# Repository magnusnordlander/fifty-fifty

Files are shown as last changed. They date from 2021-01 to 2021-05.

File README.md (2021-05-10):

# fifty-fifty
A grinder controller for my Mazzer Major

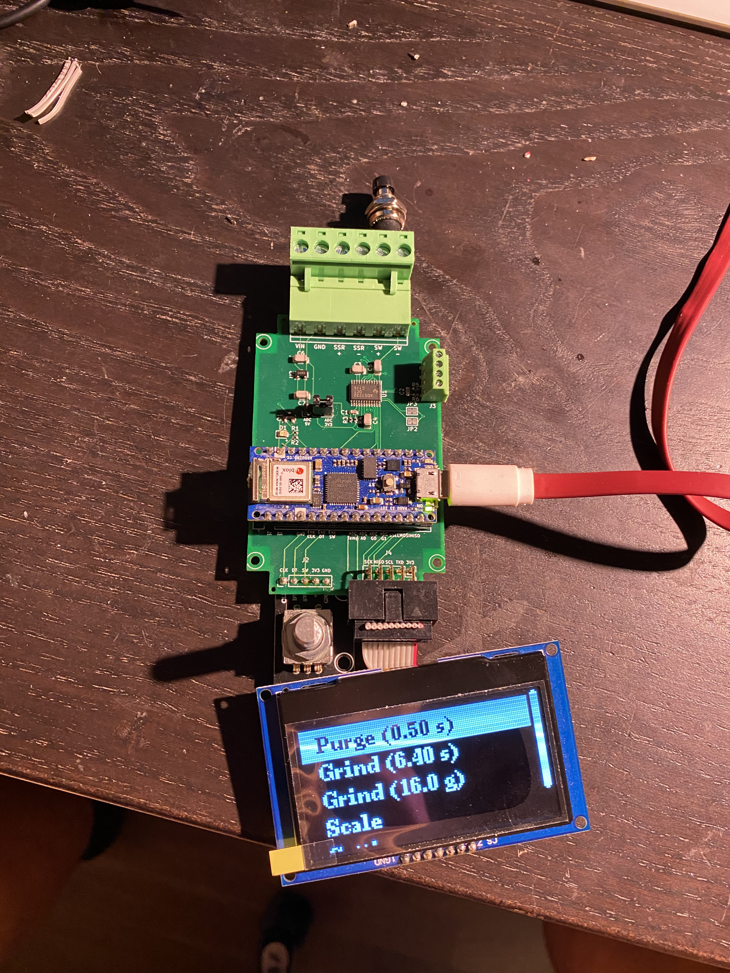
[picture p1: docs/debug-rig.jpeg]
Photo of the debug rig


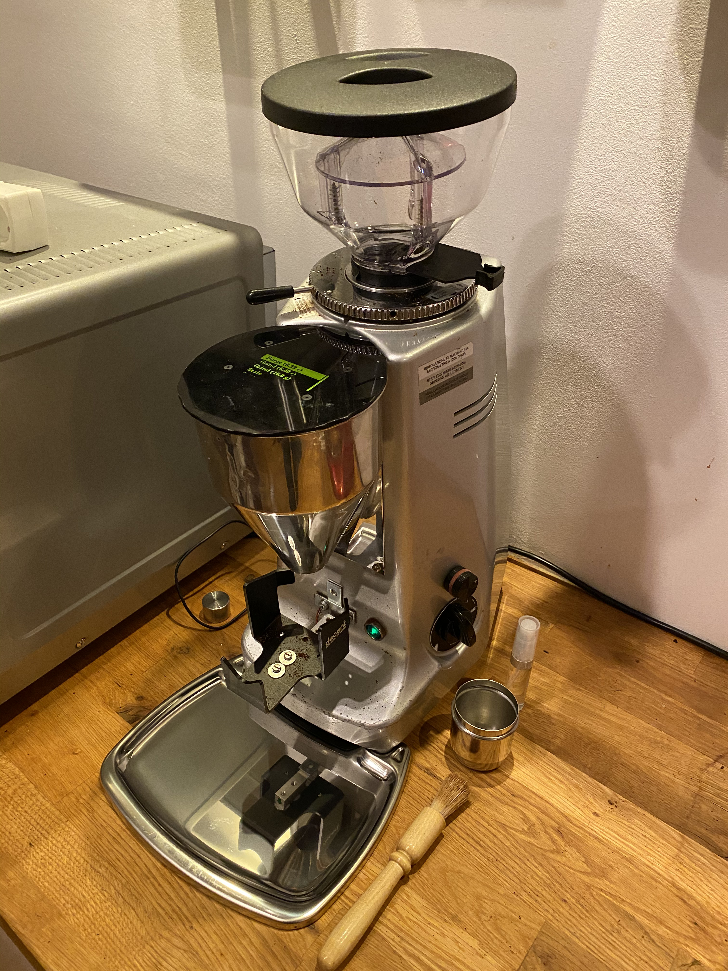
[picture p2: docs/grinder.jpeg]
Photo of the modded grinder


## Status
This project is in use and development. Current PCB Revision is Rev C.

*There will be a Rev D PCB*. The Rev D PCB will adjust the fit for a Futurekit FB20 box (it's currently slightly too large, and the mounting holes are misaligned). 

### Changelog

* Rev A: First revision board
* Rev B: Substantial changes. ADS1232 load cell interface, SMT components, fully populated UEXT connector (was printed).
  * Errata: Resistor R2 never should have existed. Remove R2 or cut trace from R2 to GND.
  * Errata: R3 and R4 silk screens are flipped around. They're the same value though, so it doesn't make any material difference.
* Rev C: Removed the resistor that was R2 in Rev B (hasn't been printed), fixed silk screen, added dots for SMT ICs.
  * Errata: Doesn't quite fit in the intended Futurekit FB20 box.

## Overview

This is an Arduino based grinder controller for my Mazzer Major. It has a display and is controlled by a rotary encoder. It also contains a PCB schematic.

## Features

* Grinder control via a simple to use interface, controlled by a rotary encoder
* Timed grinding
* Grind by weight
  * An ADS1232 load cell interface, sampling a load cell at 80 SPS.
  * High accuracy
  * Fast taring

## Parts

* [Arduino Nano 33 IoT](https://www.electrokit.com/en/product/arduino-nano-33-iot-with-headers/)
* A Solid-state relay
  * I'm using a [Fotek SSR-40 DA clone](https://www.electrokit.com/en/product/solid-state-relay-3-32v-40a/), because that's what came with my used grinder when I bought it
  * If you want a more high-quality component, a [Crydom-Sensata 84137000](http://www.crydom.com/en/products/catalog/gnssr.pdf) would be a good choice
* A high quality 5.3-6.0V power supply. I'm using a [Mean Well RS-15-5](https://www.amazon.se/gp/product/B00MWQD43U/ref=ppx_yo_dt_b_asin_title_o01_s01?ie=UTF8&psc=1). Quality matters for minimizing ADC interference. A 5V power supply with an adjustment potentiometer should do fine, the LDO will regulate anything between 5.3 and 6.0 V to 5V for the ADC. Set your PSU to 5.5V and all will be good.
* A [KY-040 style rotary encoder](https://www.electrokit.com/en/product/rotary-encoder-module/)
* An [SSD1309, SPI connected, 3.3V, 128x64 px OLED](https://www.electrokit.com/produkt/lcd-oled-2-42-12x64px-spi-i2c/)
* A [1000 g whetstone bridge load cell](https://www.electrokit.com/produkt/lastcell-1kg/)

## THT BOM

* 1 x [DIL socket 32 pin (remove 2 pins, optional but recommended)](https://www.electrokit.com/en/product/dil-socket-32-pin/) (For the Arduino)
* 1 x [PCB pin header 5.08mm 6-pole right-angle](https://www.electrokit.com/en/product/pcb-hane-5-08mm-6-pol-vinklad/) (For power, SSR and manual grind knob connection)
* 1 x [IDC box header PCB 10-p 2.54mm](https://www.electrokit.com/en/product/idc-box-header-pcb-10-p-2-54mm/) (For display connection)
* 1 x [Screw terminal 2.54mm 4-pole](https://www.electrokit.com/produkt/skruvplint-2-54mm-4-pol/) (For load cell connection)
* 1 x [5 pin 2.54mm pin header](https://www.electrokit.com/en/product/pin-header-2-54mm-1x40p-red/) (For rotary encoder connection)
* 1 x 3 pin 2.54mm pin header (For ADC debug voltage jumper)
* 1 x [2.54mm jumper](https://www.electrokit.com/produkt/bygel-2-54mm-2p-svart/)

## Anything else?

While not technically part of the board, you'll probably want some other things to make it all work:

* 1 x [Screw terminal pluggable 5.08mm 6-pole](https://www.electrokit.com/en/product/skruvplint-pluggbar-5-08mm-6-pol/)
* 1 x 10 pin IDC flat cable
* 1 x 5 pin jumper wires
* Wiring
  * 0.75 mm² (or higher) copper wiring for the high voltage side
    * Preferably in standard colors, which would be blue/brown in Europe for neutral/load. Signal wire from SSR to the motor can be any other color except green/yellow. Orange is a good choice.
  * Wiring cable, I'd go for 0.20 mm² copper. Preferably in red and black.
* WAGO 221 splicing connectors
* A 100.0 g reference weight for scale calibration

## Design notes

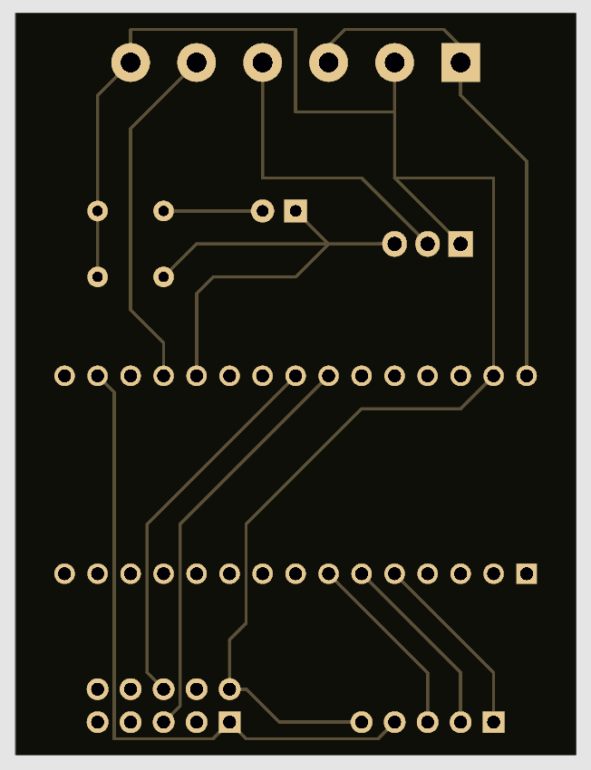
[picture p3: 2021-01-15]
pcb/Back.png

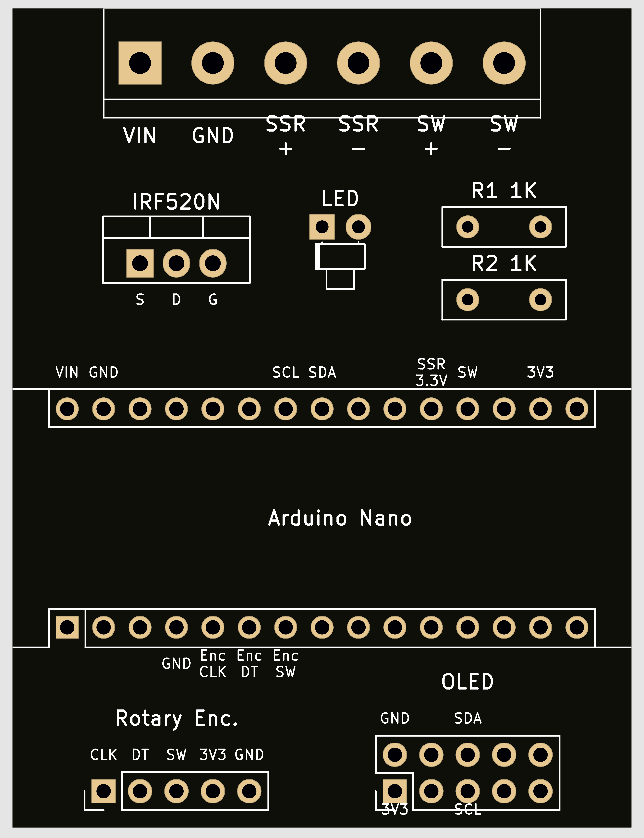
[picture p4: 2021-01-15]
pcb/Front.png

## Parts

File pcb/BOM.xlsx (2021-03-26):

Chip | Name | Package | Purpose | LCSC | Misc
U1 | ADS1232IPWR | TSSOP-24_4.4x7.8x0.65P | ADC | C27919
U2 | XC6206P502MR | SOT-23-3 | LDO | C16767
Q1 | 2N7002 | SOT-23-3 | Mosfet | C8545
D1 | FC-2012HRK-620D | LED_0805 | LED | C84256 | 2V 25 mA
R1 | 0402WGF510JTCE | 0402 | LED limiter | C25125 | 51R
R2 | 0402WGF1000TCE | 0402 | REFP filter | C25076 | 100R
R3 | 0402WGF1000TCE | 0402 | REFN filter | C25076 | 100R
R4 | 0402WGF1000TCE | 0402 | AINP1 filter | C25076 | 100R
R5 | 0402WGF1000TCE | 0402 | AINN1 filter | C25076 | 100R
C1 | CGA3E2C0G1H103JT0Y0N | 0603 | REF filter | C76710 | 10 nF, C0G
C2 | CGA3E2C0G1H103JT0Y0N | 0603 | AIN filter | C76710 | 10 nF, C0G
C3 | GRM31C5C1H104JA01L | 1206 | ADC cap | C97946 | 100 nF, C0G
C4 | GRM31C5C1H104JA01L | 1206 | AVDD filter | C97946 | 100 nF
C5 | GRM31C5C1H104JA01L | 1206 | DVDD filter | C97946 | 100 nF
C6 | GRM31C5C1H104JA01L | 1206 | LDO VI | C97946 | 100 nF
C7 | GRM31C5C1H104JA01L | 1206 | LDO VO | C97946 | 100 nF

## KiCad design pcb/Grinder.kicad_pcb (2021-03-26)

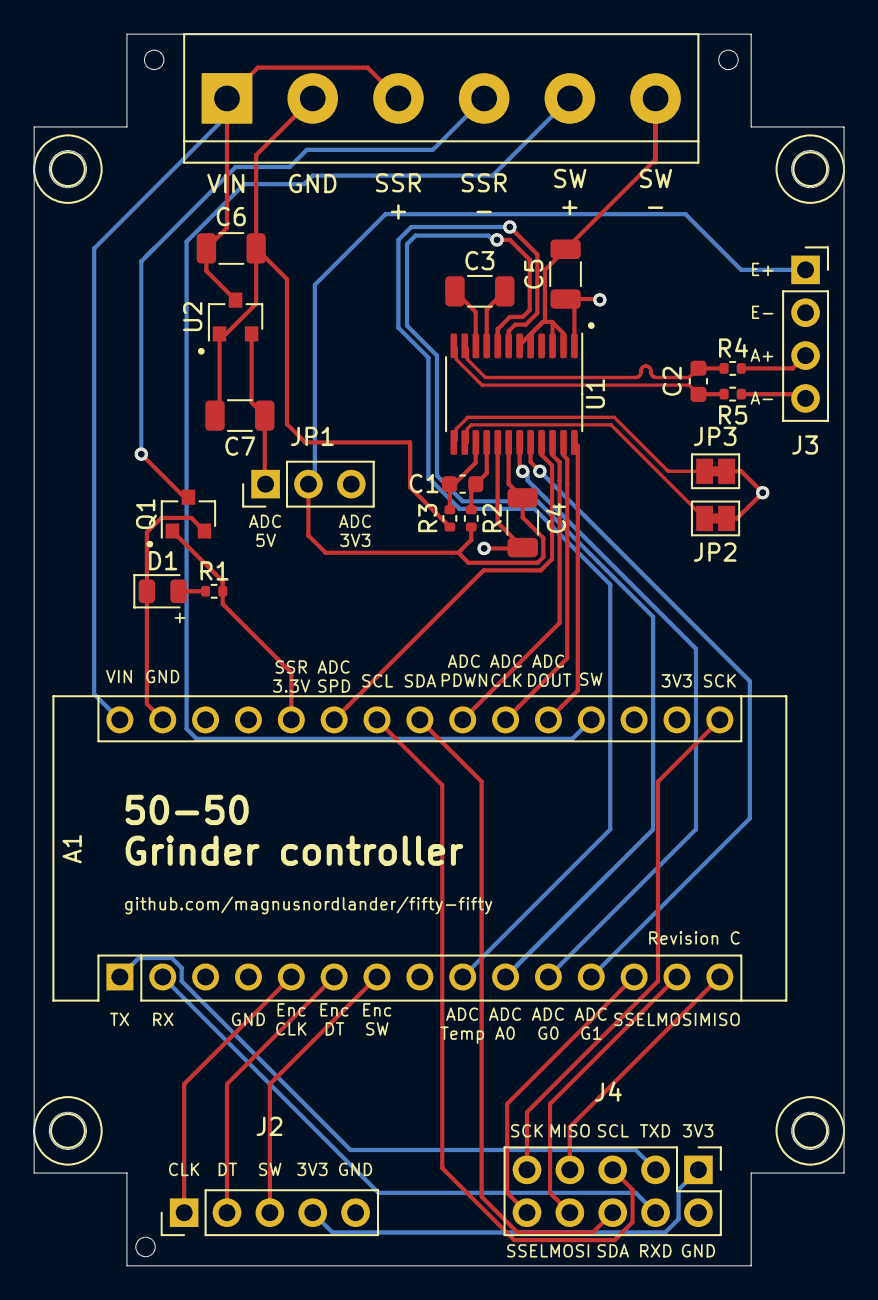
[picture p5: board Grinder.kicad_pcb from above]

Board: 4 copper layers, 48.0 x 73.0 mm, 24 parts (0 on the bottom side), 38 nets.

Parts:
A1: Arduino Nano 33 IoT; Arduino_Nano
C1, C2: 10 nF; C_0603_1608Metric
C3, C5, C6, C7: 100 nF; C_1206_3216Metric
C4: 100nF; C_1206_3216Metric
D1: LED; LED_0805_2012Metric
J1: Conn_01x06; TerminalBlock_bornier-6_P5.08mm
J2: Conn_01x05; PinHeader_1x05_P2.54mm_Vertical
J3: Conn_01x04; PinSocket_1x04_P2.54mm_Vertical
J4: Conn_02x05_Odd_Even; PinHeader_2x05_P2.54mm_Vertical
JP1: Debug voltage; PinHeader_1x03_P2.54mm_Vertical
JP2: AINP2; SolderJumper-2_P1.3mm_Bridged_Pad1.0x1.5mm
JP3: AINN2; SolderJumper-2_P1.3mm_Bridged_Pad1.0x1.5mm
Q1: 2N7002; SOT-23
R1: R; R_0402_1005Metric
R2, R3, R4, R5: 100R; R_0402_1005Metric
U1: ADS1232IPW; TSSOP-24_4.4x7.8mm_P0.65mm
U2: XC6206P502MR; SOT-23

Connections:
3V3: A1.17, C5.1, J2.4, J4.1, JP1.3, U1.1
ADC_A0: A1.10, U1.8
ADC_CLK: A1.21, U1.23
ADC_DOUT: A1.20, U1.24
ADC_GAIN0: A1.11, U1.19
ADC_GAIN1: A1.12, U1.20
ADC_PDWN: A1.22, U1.22
ADC_SPEED: A1.25, U1.21
ADC_TEMP: A1.9, U1.7
AIN1_N: C2.2, R5.1, U1.12
AIN1_P: C2.1, R4.1, U1.11
AIN2_N: JP3.2, U1.13
AIN2_P: JP2.2, U1.14
AVDD: C4.2, J3.1, JP1.2, R2.2, U1.18
ENC_CLK: A1.5, J2.1
ENC_DT: A1.6, J2.2
ENC_SW: A1.7, J2.3
GND: A1.4, A1.29, C4.1, C5.2, C6.2, C7.2, D1.1, J1.2, J1.6, J2.5, J3.2, J4.2, JP2.1, JP3.1, Q1.2, R3.2, U1.2, U1.3, U1.5, U1.6, U1.17, U2.1
MANUAL_SW: A1.19, J1.5
unnamed: C3.1, U1.9
unnamed: C3.2, U1.10
unnamed: C7.1, JP1.1, U2.2
unnamed: D1.2, R1.1
unnamed: J3.3, R4.2
unnamed: J3.4, R5.2
REFN: C1.2, R3.1, U1.15
REFP: C1.1, R2.1, U1.16
SSR_DRAIN: J1.4, Q1.3
SSR_GATE: A1.26, Q1.1, R1.2
UEXT_MISO: A1.15, J4.7
UEXT_MOSI: A1.14, J4.8
UEXT_RX: A1.2, J4.4
UEXT_SCK: A1.16, J4.9
UEXT_SCL: A1.24, J4.5
UEXT_SDA: A1.23, J4.6
UEXT_SSEL: A1.13, J4.10
UEXT_TX: A1.1, J4.3
VIN: A1.30, C6.1, J1.1, J1.3, U2.3

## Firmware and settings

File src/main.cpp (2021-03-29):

#include <Arduino.h>
#include <U8g2lib.h>
#include <Wire.h>
#include <Encoder.h>
#include "NavigationController.h"
#include "ViewControllers/Menus/MenuViewController.h"
#include "ViewControllers/Grinding/ManualGrindViewController.h"
#include "ViewControllers/Settings/PurgeTimeSettingViewController.h"
#include "ViewControllers/Settings/GrindTimeSettingViewController.h"
#include "ViewControllers/Settings/GrindTargetWeightSettingViewController.h"
#include "ViewControllers/Settings/ReactionTimeSettingViewController.h"
#include "ViewControllers/Settings/ScaleDebugViewController.h"
#include "ViewControllers/Grinding/GravimetricGrindViewController.h"
#include "ViewControllers/Settings/ProductivitySettingViewController.h"
#include "ViewControllers/Settings/CalibrationViewController.h"
#include "ViewControllers/Settings/PerformanceDebugViewController.h"
#include "ViewControllers/Grinding/PurgeViewController.h"
#include "ViewControllers/Grinding/TimedGrindViewController.h"
#include "ViewControllers/ScaleViewController.h"
#include "ViewControllers/Menus/MenuItem/ViewControllerMenuItem.h"
#include "ViewControllers/Menus/MenuItem/PopNavigationAndCommitEEPROMMenuItem.h"
#include "ViewControllers/Menus/MenuItem/PurgeMenuItem.h"
#include "ViewControllers/Menus/MenuItem/GrindMenuItem.h"
#include "ViewControllers/Menus/MenuItem/GrindByWeightMenuItem.h"
#include "Settings.h"
#include "ScaleWrapper.h"
#include "ViewControllers/ButtonEvent.h"
#include <types.h>

// DT and CLK must be interrupt pins
#define ENCODER_SW_PIN 4
#define ENCODER_DT_PIN 3
#define ENCODER_CLK_PIN 2

#define MANUAL_GRIND_PIN 14

#define SSR_PIN 21

// DOUT must be interrupt pin
#define ADS1232_PWDN_PIN 17
#define ADS1232_DOUT_PIN 15
#define ADS1232_SCLK_PIN 16
#define ADS1232_TEMP_PIN 6
#define ADS1232_A0_PIN 7
#define ADS1232_GAIN0_PIN 8
#define ADS1232_GAIN1_PIN 9
#define ADS1232_SPEED_PIN 20

// With the exception of CS, these pins are hardware supported
#define UEXT_SPI_CS_PIN 10
#define UEXT_SPI_SCK_PIN 13
#define UEXT_SPI_MISO_PIN 12
#define UEXT_SPI_MOSI_PIN 11
#define UEXT_I2C_SCL_PIN 19
#define UEXT_I2C_SDA_PIN 18

#define SCROLL_DIRECTION 1
// Use I2C SCL as SSD1309 DC and I2C SDA as SSD1309 RES
U8G2_SSD1309_128X64_NONAME0_F_4W_HW_SPI u8g2(U8G2_R2, UEXT_SPI_CS_PIN, UEXT_I2C_SCL_PIN, UEXT_I2C_SDA_PIN);

int Encoder_SW_State = 0;
long Encoder_Diff = 0;
int Manual_Grind_State = HIGH;

long Old_Encoder_Position  = 0;

microtime_t Button_Press_Started_At = 0;

ButtonEvent currentButtonEvent = BUTTON_INACTIVE;

Encoder myEnc(ENCODER_DT_PIN, ENCODER_CLK_PIN);

ScaleWrapper* scale;
SsrState* ssr = nullptr;
ManualGrindViewController* manualGrindView = nullptr;
NavigationController* nav = nullptr;

TimingStruct timings;

void setup(void) {
    pinMode(MANUAL_GRIND_PIN, INPUT_PULLUP);
    pinMode(ENCODER_SW_PIN, INPUT_PULLUP);

    u8g2.begin();

/*
    delay(5000);
    Serial.begin(9600);
    Serial.println("Starting");
    */

    ssr = new SsrState(SSR_PIN);
    auto settings = new Settings();

    pinMode(ADS1232_TEMP_PIN, OUTPUT);
    pinMode(ADS1232_A0_PIN, OUTPUT);
    pinMode(ADS1232_GAIN0_PIN, OUTPUT);
    pinMode(ADS1232_GAIN1_PIN, OUTPUT);
    pinMode(ADS1232_SPEED_PIN, OUTPUT);

    digitalWrite(ADS1232_TEMP_PIN, LOW);
    digitalWrite(ADS1232_A0_PIN, LOW);
    digitalWrite(ADS1232_GAIN0_PIN, HIGH);
    digitalWrite(ADS1232_GAIN1_PIN, HIGH);
    digitalWrite(ADS1232_SPEED_PIN, HIGH);

    scale = ScaleWrapper::GetInstance(ADS1232_DOUT_PIN, ADS1232_SCLK_PIN, ADS1232_PWDN_PIN, settings);

    manualGrindView = new ManualGrindViewController(ssr);

    auto settingsMenu = new MenuViewController(std::vector<MenuItem*> {{
            new ViewControllerMenuItem("Purge time", new PurgeTimeSettingViewController(settings)),
            new ViewControllerMenuItem("Grind time", new GrindTimeSettingViewController(settings)),
            new ViewControllerMenuItem("Target weight", new GrindTargetWeightSettingViewController(settings)),
            new ViewControllerMenuItem("Reaction time", new ReactionTimeSettingViewController(settings)),
            new ViewControllerMenuItem("Productivity", new ProductivitySettingViewController(settings)),
            new ViewControllerMenuItem("Calibrate (100 g)", new CalibrationViewController(settings, scale)),
            new ViewControllerMenuItem("Scale debug", new ScaleDebugViewController(scale)),
            new ViewControllerMenuItem("Performance debug", new PerformanceDebugViewController()),
            new PopNavigationAndCommitEEPROMMenuItem("Back", settings)
    }});

    auto mainMenu = new MenuViewController(std::vector<MenuItem*> {{
            new PurgeMenuItem(new PurgeViewController(ssr, settings), settings),
            new GrindMenuItem(new TimedGrindViewController(ssr, settings), settings),
            new GrindByWeightMenuItem(new GravimetricGrindViewController(ssr, scale, settings), settings),
            new ViewControllerMenuItem("Scale", new ScaleViewController(scale)),
            new ViewControllerMenuItem("Settings...", settingsMenu),
    }});

    nav = new NavigationController(mainMenu);
}

void updateExternalState() {
    Encoder_Diff = 0;
    long new_encoder_position = myEnc.read();
    if (new_encoder_position != Old_Encoder_Position) {
        Encoder_Diff = (new_encoder_position/4 - Old_Encoder_Position/4);
        #ifdef DEBUG_RIG
        //Serial.println(Encoder_Diff);
        #endif
        Old_Encoder_Position = new_encoder_position;
    }

    Encoder_SW_State = digitalRead(ENCODER_SW_PIN);
    Manual_Grind_State = digitalRead(MANUAL_GRIND_PIN);

    if (Button_Press_Started_At == 0 && Encoder_SW_State == LOW) {
        Button_Press_Started_At = micros();
        currentButtonEvent = BUTTON_PRESS;
    } else if (Button_Press_Started_At > 0 && Encoder_SW_State == LOW) {
        currentButtonEvent = BUTTON_HOLD;
    } else if (Button_Press_Started_At > 0 && Encoder_SW_State == HIGH) {
        microtime_t holdLength = micros() - Button_Press_Started_At;
        if (holdLength > 300000) {
            currentButtonEvent = BUTTON_PRESS_AND_HOLD_LET_UP;
        } else {
            currentButtonEvent = BUTTON_LET_UP;
        }
        Button_Press_Started_At = 0;
    } else { // (Button_Press_Started_At == 0 && Encoder_SW_State == HIGH) {
        currentButtonEvent = BUTTON_INACTIVE;
    }

    scale->refresh();
}

void loop(void) {
    microtime_t start = micros();

    BaseViewController* top = nav->top();

    microtime_t externalStart = micros();
    updateExternalState();

    microtime_t manualStart = micros();
    // Handle manual grind state
    if (top != manualGrindView && Manual_Grind_State == LOW) {
        nav->push(manualGrindView);
    } else if (top == manualGrindView && Manual_Grind_State == HIGH) {
        nav->pop();
    }

    microtime_t buttonStart = micros();
    nav->top()->handleButtonEvent(currentButtonEvent);

    microtime_t rotationStart = micros();
    if (currentButtonEvent == BUTTON_INACTIVE) {
        if (Encoder_Diff != 0) {
            nav->top()->handleRotation(Encoder_Diff * SCROLL_DIRECTION);
        }
    }

    microtime_t tickStart = micros();
    nav->top()->tick(u8g2);

    microtime_t end = micros();

    timings = (TimingStruct){
        .external = manualStart - externalStart,
        .manual = rotationStart - manualStart,
        .rotation = buttonStart - rotationStart,
        .button = tickStart - buttonStart,
        .tick = end - tickStart,
        .loop = end - start,
    };
}

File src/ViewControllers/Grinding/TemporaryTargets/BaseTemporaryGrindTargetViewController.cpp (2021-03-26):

//
// Created by Magnus Nordlander on 2021-02-14.
//

#include "BaseTemporaryGrindTargetViewController.h"
#include <Utils/TextUtils.h>

void BaseTemporaryGrindTargetViewController::handleRotation(int encoderDiff) {
    int amplified_encoder_diff = encoderDiff * this->settingSensitivity;

    if (amplified_encoder_diff != 0) {
        if (this->target + amplified_encoder_diff > USHRT_MAX) {
            this->target = USHRT_MAX;
        }
        else if (this->target + amplified_encoder_diff < 0) {
            this->target = 0;
        } else {
            this->target += amplified_encoder_diff;
        }
    }
}

BaseTemporaryGrindTargetViewController::BaseTemporaryGrindTargetViewController(Settings *settings) : settings(settings) {}

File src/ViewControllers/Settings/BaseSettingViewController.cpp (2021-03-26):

//
// Created by Magnus Nordlander on 2021-02-07.
//

#include "BaseSettingViewController.h"

void BaseSettingViewController::handleRotation(int encoderDiff) {
    int amplified_encoder_diff = encoderDiff * this->settingSensitivity;

    if (amplified_encoder_diff != 0) {
        if (this->target + amplified_encoder_diff > USHRT_MAX) {
            this->target = USHRT_MAX;
        }
        else if (this->target + amplified_encoder_diff < 0) {
            this->target = 0;
        } else {
            this->target += amplified_encoder_diff;
        }
    }
}

BaseSettingViewController::BaseSettingViewController(Settings *settings) : settings(settings) {
    this->target = 0;
}

void BaseSettingViewController::viewWasPushed(NavigationController *controller) {
    BaseViewController::viewWasPushed(controller);
    this->target = this->getTargetFromSettings();
}

void BaseSettingViewController::viewWillBePopped(NavigationController *controller) {
    this->stageTargetInSettings(this->target);
    BaseViewController::viewWillBePopped(controller);
}

unsigned short BaseSettingViewController::getTargetFromSettings() {
    return 0;
}

void BaseSettingViewController::stageTargetInSettings(unsigned short) {

}

void BaseSettingViewController::handleButtonEvent(ButtonEvent event) {
    if (event == BUTTON_LET_UP) {
        this->navigationController->pop();
    }
}

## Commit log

2021-01-09 Initial import
    [Grinder.kicad_pcb, Grinder.sch]
2021-02-13 Switched to an interrupt based scale system and added a calibration routine
2021-02-13 Refactored button handling
2021-02-21 Fixed bugs with scale and print rate of change
2021-02-21 Fixed timer wraparound issues
2021-02-24 WIP for new PCB
    [BOM.xlsx, Grinder.kicad_pcb]
2021-02-27 Handle rotation after button handling, and only if we’re not interacting with the button
2021-03-04 Changed IRLZ44N for 2N7002
    [BOM.xlsx, Grinder.kicad_pcb, Grinder.sch]
2021-03-06 Final changes before ordering PCB
    [BOM.xlsx, Grinder.kicad_pcb, Grinder.sch]
2021-03-06 Updated pin assignments for the ordered rev-b board
2021-03-26 Updated to revision C PCB
    [BOM.xlsx, Grinder.kicad_pcb, Grinder.sch]
2021-03-29 Scale refactor (#1)
    * Updated gitignore
    * WIP
    * Fixed stuff
    * Tweaks
    * Tweaks
    * More tweaks
    [main.cpp]
